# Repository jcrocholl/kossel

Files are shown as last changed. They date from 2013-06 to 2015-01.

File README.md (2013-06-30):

Release status
==============

Most of these parts are now stable and won't change much more.

How to print Mini Kossel
========================

* 3x plate_3x.stl (about 3x80g = 240g of plastic)
* 1x plate_1x.stl (about 50g of plastic)

Links
=====

* Bill of Materials: http://reprap.org/wiki/Kossel
* Mailing list: http://groups.google.com/group/deltabot
* Project history: http://deltabot.tumblr.com

Pay it forward
==============

Johann is offering free printed parts for Mini Kossel:

* I'm going to make some Mini Kossel printed parts kits.
* I'm going to give them away for free (as in beer).
* Some kits may include some non-printed parts.
* Free international shipping is included.
* No delivery schedule, maybe only one kit per month.

But there's no such thing as a free lunch. If you want to receive a
free kit, you must swear by your geek honor:

* To complete your Mini Kossel and tune it well.
* To print two (2) Mini Kossel kits and also give them away for free.
* To make your recipients agree to the same rule.

After giving away the 2 free kits, you may sell printed parts for any
price you want.

If you're interested, please email johann@rocholl.net and let me know
your favorite PLA color and mailing address. If you want to get your
printed parts first, explain why you're more qualified than others to
start giving away high quality printed parts soon.

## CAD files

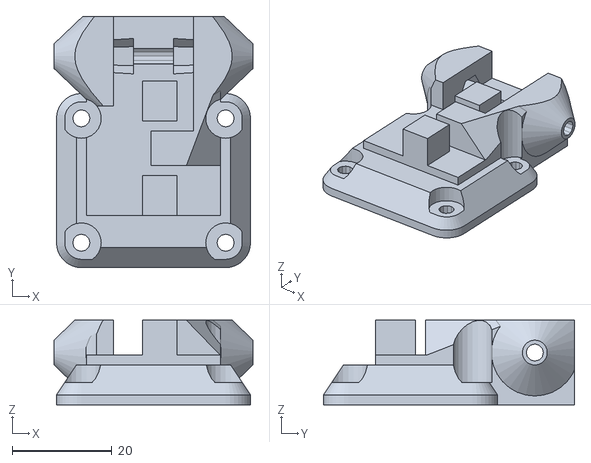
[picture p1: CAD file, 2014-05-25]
carriage_recirculating.stl
40.0 x 50.5 x 17.0

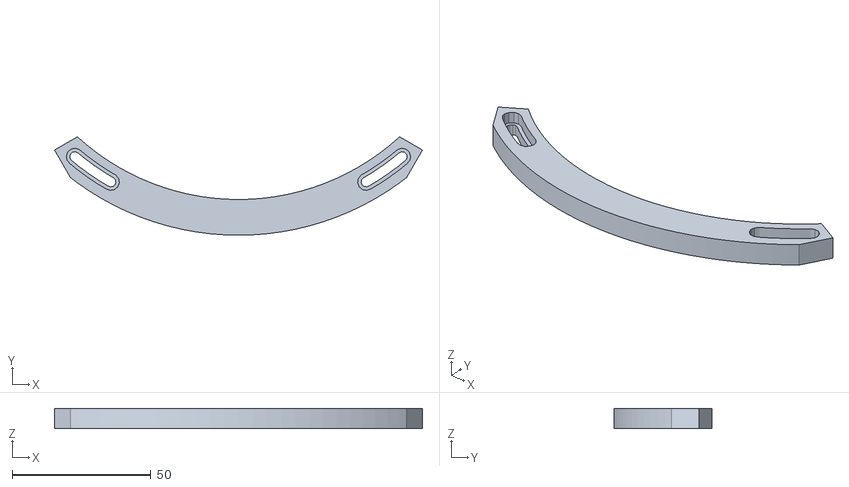
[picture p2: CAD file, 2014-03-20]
glass_frame.stl
132.8 x 35.5 x 7.35

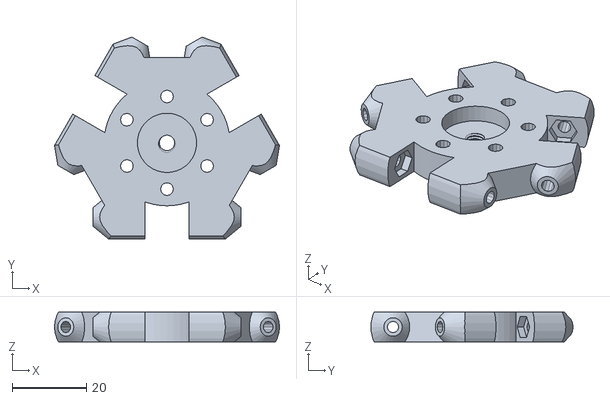
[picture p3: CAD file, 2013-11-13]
effector.stl
60.7 x 54.5 x 8.00

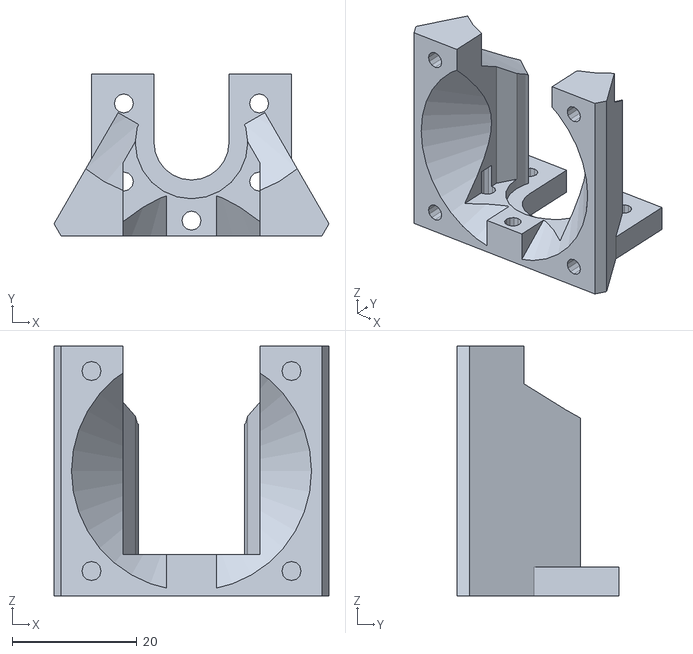
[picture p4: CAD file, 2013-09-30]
hotend_fan.stl
44.0 x 26.0 x 40.0

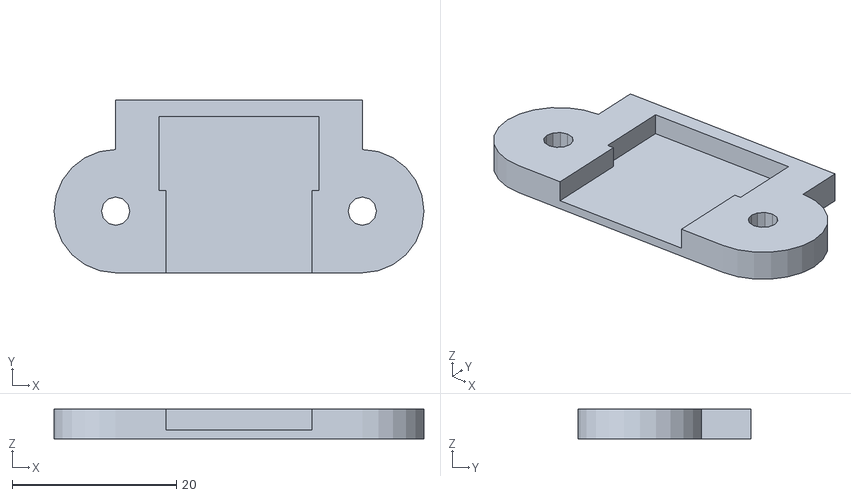
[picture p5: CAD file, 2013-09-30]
switch_holder.stl
45.0 x 21.0 x 3.60

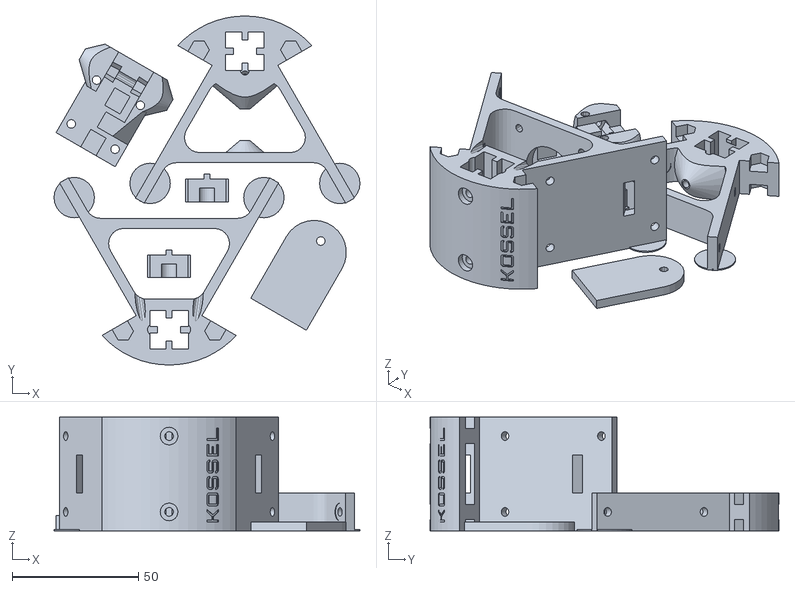
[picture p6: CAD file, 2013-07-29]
plate_3x.stl
121.0 x 138.0 x 45.0

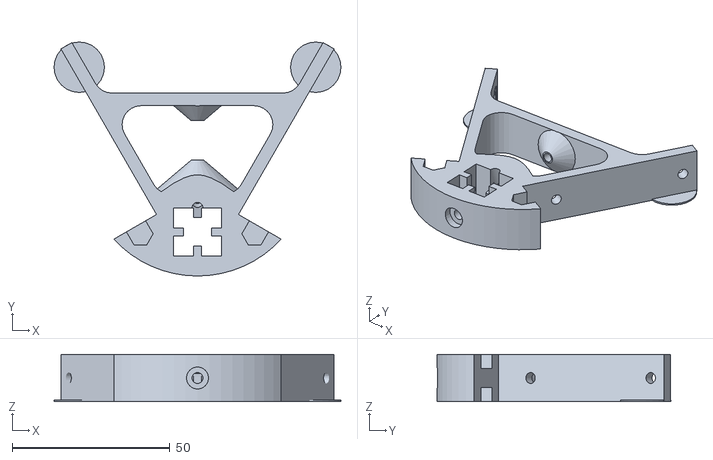
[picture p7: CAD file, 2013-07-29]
frame_top.stl
91.0 x 74.2 x 15.0

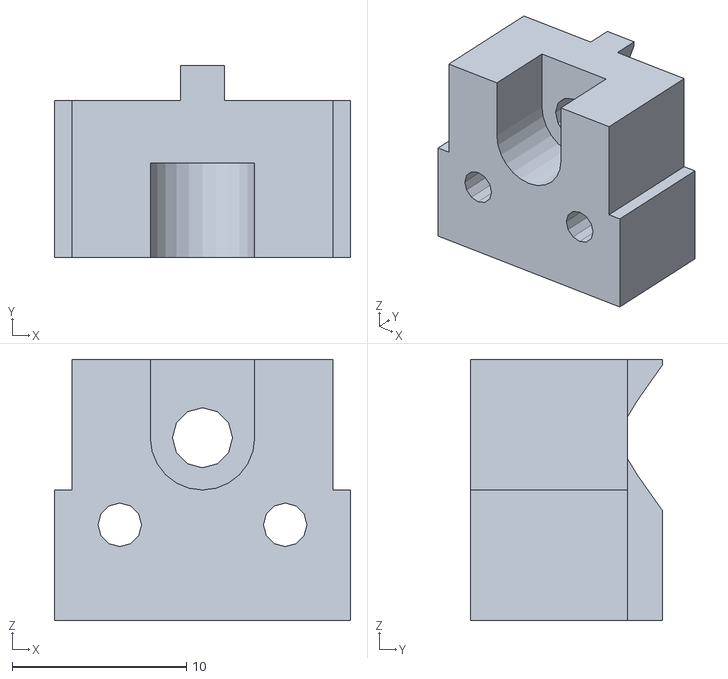
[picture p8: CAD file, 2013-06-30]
endstop.stl
17.0 x 11.0 x 15.0

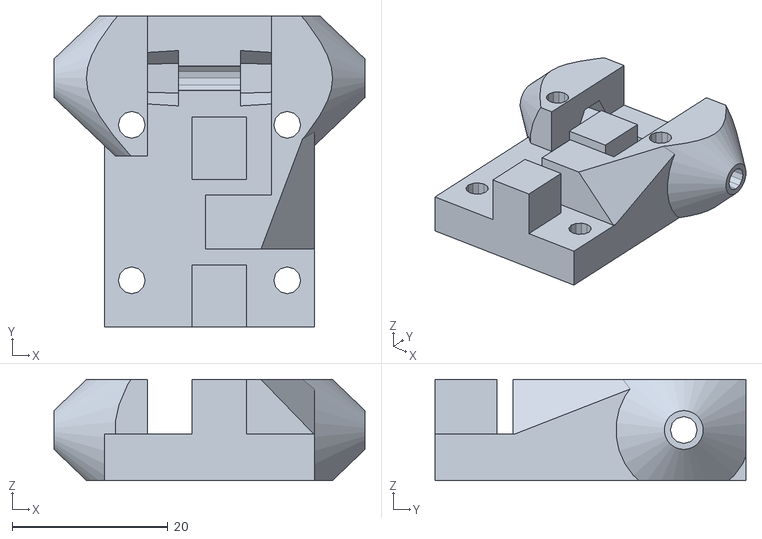
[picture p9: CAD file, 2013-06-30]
carriage.stl
40.0 x 40.0 x 13.0

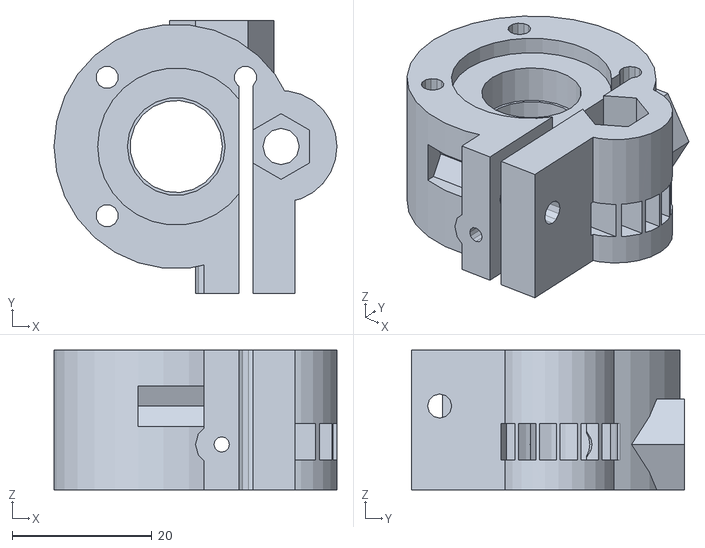
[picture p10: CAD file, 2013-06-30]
extruder.stl
40.5 x 39.0 x 20.0

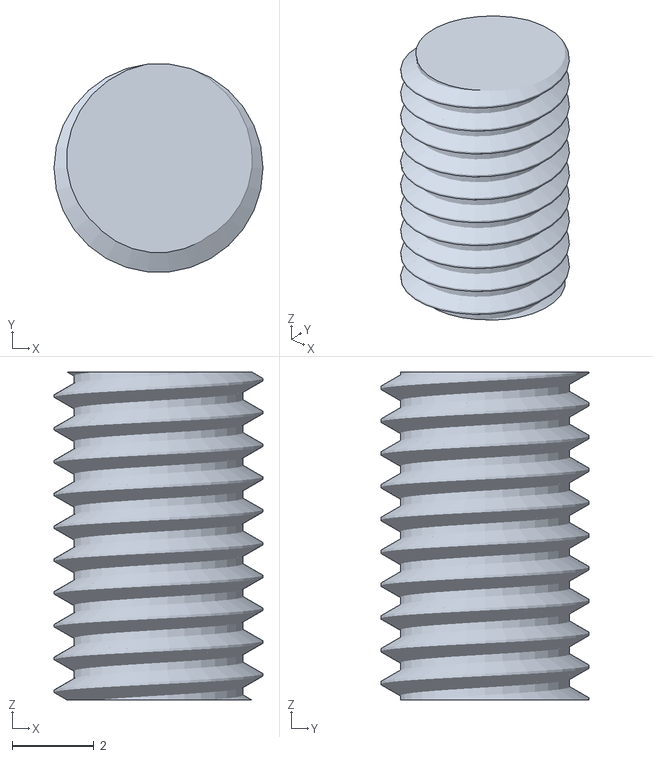
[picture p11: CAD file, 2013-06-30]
m5_internal.stl
5.10 x 5.07 x 8.00

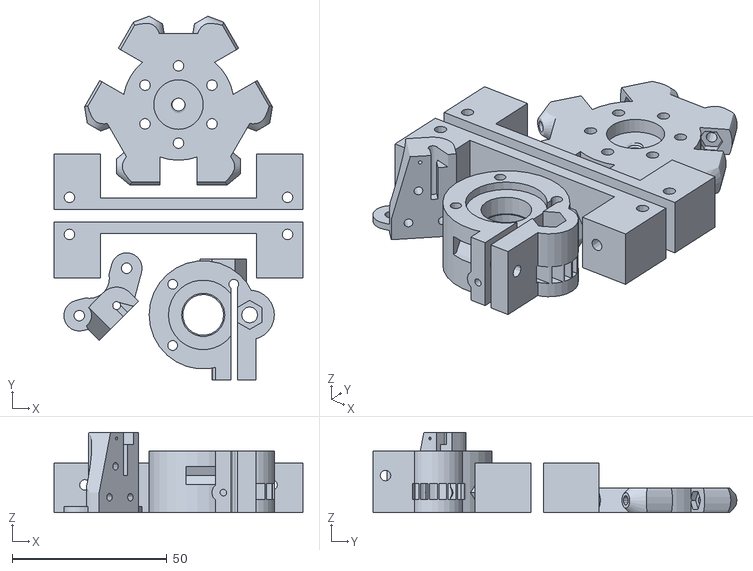
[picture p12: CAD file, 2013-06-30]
plate_1x.stl
80.5 x 117.6 x 26.0

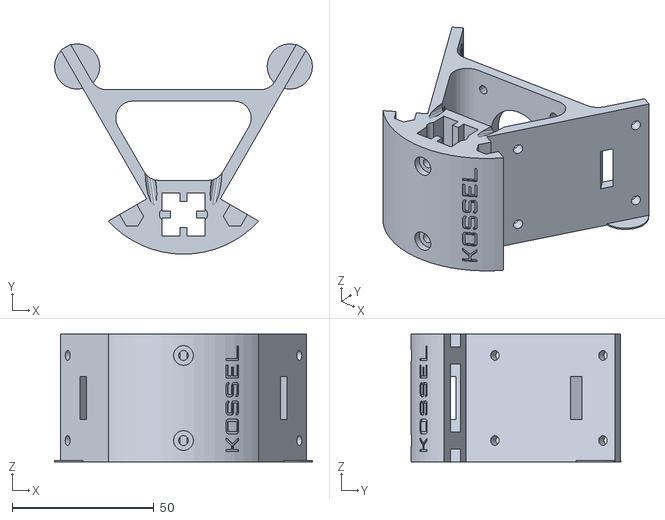
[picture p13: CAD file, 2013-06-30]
frame_motor.stl
91.0 x 74.2 x 45.0

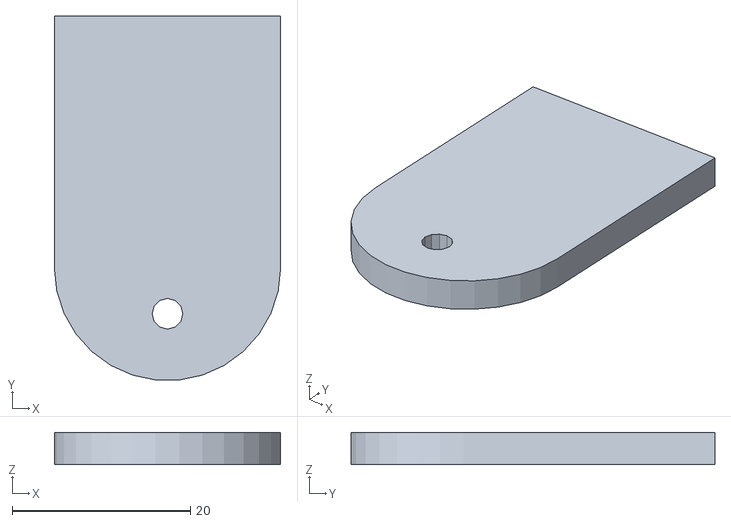
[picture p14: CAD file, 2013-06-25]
glass_tab.stl
25.4 x 40.8 x 3.60

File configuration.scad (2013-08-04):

// Increase this if your slicer or printer make holes too tight.
extra_radius = 0.1;

// OD = outside diameter, corner to corner.
m3_nut_od = 6.1;
m3_nut_radius = m3_nut_od/2 + 0.2 + extra_radius;
m3_washer_radius = 3.5 + extra_radius;

// Major diameter of metric 3mm thread.
m3_major = 2.85;
m3_radius = m3_major/2 + extra_radius;
m3_wide_radius = m3_major/2 + extra_radius + 0.2;

// NEMA17 stepper motors.
motor_shaft_diameter = 5;
motor_shaft_radius = motor_shaft_diameter/2 + extra_radius;

// Frame brackets. M3x8mm screws work best with 3.6 mm brackets.
thickness = 3.6;

// OpenBeam or Misumi. Currently only 15x15 mm, but there is a plan
// to make models more parametric and allow 20x20 mm in the future.
extrusion = 15;

// Placement for the NEMA17 stepper motors.
motor_offset = 44;
motor_length = 47;

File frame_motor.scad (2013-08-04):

include <configuration.scad>;

use <vertex.scad>;
use <nema17.scad>;

$fn = 24;

module frame_motor() {
  difference() {
    // No idler cones.
    vertex(3*extrusion, idler_offset=0, idler_space=100);
    // KOSSEL logotype.
    translate([20.5, -10, 0]) rotate([90, -90, 30])
      scale([0.11, 0.11, 1]) import("logotype.stl");
    // Motor cable paths.
    for (mirror = [-1, 1]) scale([mirror, 1, 1]) {
      translate([-35, 45, 0]) rotate([0, 0, -30])
        # cube([4, 15, 15], center=true);
      translate([-6, 0, 0]) cylinder(r=2.5, h=40);
      translate([-11, 0, 0]) # cube([15, 4, 15], center=true);
    }
    translate([0, motor_offset, 0]) {
      // Motor shaft/pulley cutout.
      rotate([90, 0, 0]) cylinder(r=12, h=20, center=true, $fn=60);
      // NEMA 17 stepper motor mounting screws.
      for (x = [-1, 1]) for (z = [-1, 1]) {
        scale([x, 1, z]) translate([15.5, -5, 15.5]) {
          rotate([90, 0, 0]) cylinder(r=1.65, h=20, center=true, $fn=12);
          // Easier ball driver access.
          rotate([74, -30, 0]) # cylinder(r=1.8, h=60, $fn=12);
        }
      }
    }
    translate([0, motor_offset, 0]) rotate([90, 0, 0]) % nema17();
  }
}

translate([0, 0, 22.5]) frame_motor();

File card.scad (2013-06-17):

scale([-1, 1, 1]) difference() {
  minkowski() {
    cube([66, 29, 0.2], center=true);
    cylinder(r=10, h=0.2, $fn=24);
  }
  difference() {
    translate([1, -4, 0]) scale([0.2, 0.2, 1]) import("logotype.stl");
    # translate([-17.2, 0, 0]) cube([1, 20, 20], center=true);
  }
}

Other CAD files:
frame_extruder.stl
logotype.stl
power_supply.stl
retractable.stl
carriage.scad
Orbitron_Medium.scad
card.stl
carriage_recirculating.scad
effector.scad
endstop.scad
extruder.scad
frame_extruder.scad
frame_power_supply.scad
frame_top.scad
glass_frame.scad
glass_tab.scad
hotend_fan.scad
logotype.scad
m5_internal.scad
microswitch.scad
nema17.scad
pg35l_extruder.scad
plate_1x.scad
plate_3x.scad
power_supply.scad
retractable.scad
spool.scad
switch_holder.scad
threads.scad
vertex.scad

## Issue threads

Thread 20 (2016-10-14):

Kossel Mini Bed Level Problem

grimes27, 2016-10-14:
I'm very new to this but, I have my Kossel Mini up and running my only problem is it seems if I run the auto-level before I start printing it doesn't do anything because the extruder is running into the bed.  From all the checking I've done my print bed is very level but if I put my extruder at 1mm above the print bed and move the extruder roughly 40mm in any direction X+, X-, Y+ or Y- it runs into the print bed.  So either I have a convex lens for a printbed, which I doubt, because I have the same problem if I flip the bed around, or the motion of my printer is out of whack.  Any ideas what's going on or how to fix this?

kd0aij, 2016-10-14:
This is not actually an issue with the code. It sounds more like you skipped a critical part of the calibration process. Look at step #3 here: http://ladvien.github.io/robots/kossel-mini-calibration/ for adjusting delta_radius. (I just did a quick google search; you didn't mention which firmware you are using)

grimes27, 2016-10-14:
Yes, I didn't have these instructions when I set up my kossel.  I used the
one from Blomker industries and they didn't say anything about the concave
or convex surface.  Thank you very much for this.  I am using Marlin
Firmware too!

On Fri, Oct 14, 2016 at 12:16 PM, Mark Whitehorn <notifications@github.com>
wrote:

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

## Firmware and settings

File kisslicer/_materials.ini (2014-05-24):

[Rostock PLA]
g_code_matl=3B204D617962652073657420736F6D65206D6174657269616C2D737065636966696320472D636F64653F
fan_Z_mm=0.5
fan_loops_percent=100
fan_inside_percent=0
fan_cool_percent=100
temperature_C=185
keep_warm_C=120
first_layer_C=195
bed_C=0
sec_per_C_per_C=0.00964207
flow_min_mm3_per_s=0.1
flow_max_mm3_per_s=20
destring_suck=8
destring_prime=8
destring_min_mm=3
destring_trigger_mm=20
destring_speed_mm_per_s=80
Z_lift_mm=0.2
min_layer_time_s=15
wipe_mm=3
cost_per_cm3=0
flowrate_tweak=1
fiber_dia_mm=1.75
color=4288872448

[Mini Kossel PLA]
g_code_matl=3B204D617962652073657420736F6D65206D6174657269616C2D737065636966696320472D636F64653F
fan_Z_mm=0.5
fan_loops_percent=100
fan_inside_percent=0
fan_cool_percent=100
temperature_C=230
keep_warm_C=120
first_layer_C=240
bed_C=0
sec_per_C_per_C=0.00964207
flow_min_mm3_per_s=0.1
flow_max_mm3_per_s=20
destring_suck=10
destring_prime=10
destring_min_mm=2
destring_trigger_mm=20
destring_speed_mm_per_s=100
Z_lift_mm=0.2
min_layer_time_s=15
wipe_mm=3
cost_per_cm3=0
flowrate_tweak=1
fiber_dia_mm=1.75
color=4288872448

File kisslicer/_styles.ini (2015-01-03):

[Mini Kossel]
layer_thickness_mm=0.2
extrusion_width_mm=0.4
num_loops=3
skin_thickness_mm=0.6
infill_extrusion_width=0.35
infill_density_denominator=1
stacked_layers=1
use_destring=1
use_wipe=1
loops_insideout=1
infill_st_oct_rnd=0
inset_surface_xy_mm=0.1
seam_jitter_degrees=10
seam_depth_scaler=1

[Rostock]
layer_thickness_mm=0.2
extrusion_width_mm=0.5
num_loops=3
skin_thickness_mm=0.8
infill_extrusion_width=0.5
infill_density_denominator=1
stacked_layers=1
use_destring=1
use_wipe=1
loops_insideout=1
infill_st_oct_rnd=0
inset_surface_xy_mm=0
seam_jitter_degrees=60
seam_depth_scaler=1

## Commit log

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2012-09-29 Spool for fishing line on NEMA17 stepper with M3x8 screws.
    [spool.scad]
2012-09-30 Slic3r 0.9.3 doesn't need oversized holes like 0.8.4 did.
    [spool.scad]
2012-10-03 Adjustments for Slic3r 0.9.3 which seems to make more accurate parts than 0.8.4.
    [corner.scad, frame_motor.scad, spool.scad]
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2012-10-10 Diagonal filament tunnel to spool from the edge to the middle.
    [spool.scad]
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2012-10-14 Improved OpenBeam roller with 4 horizontal adjustment screws and integrated attachment for ball joints.
    [roller.scad]
2012-10-14 Added adjustable endstop screw to roller, adjusted holes.
    [roller.scad]
2012-10-18 Separate fishline tunnel parallel to motor shaft, to improve centering accuracy.
    [spool.scad]
2012-10-18 Removed some plastic that was obstructing the range of motion for the ball joints.
    [roller.scad]
2012-10-18 New triangle (quasi-L-shaped) frame vertex for top corners.
    [frame_cheek.scad]
2012-10-19 Put the adjustable endstop screw on the outside.
    [roller.scad]
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2012-10-21 Added ZM micro switch holder on the cheek outside.
    [frame_cheek.scad]
2012-10-21 Added slightly more plastic around the ball joint attachment.
    [roller.scad]
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2012-10-29 Adjusted corner screw holes for thicker 3.6mm brackets.
    [corner.scad]
2012-11-01 New fishline tensioner with a regular cheap 608 bearing (not flanged).
    [tensioner_608.scad]
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2012-11-05 Tightened M3 nut trap and OpenBeam groove clip.
    [configuration.scad, tensioner_608.scad]
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2012-11-12 Increased thickness to 3.6mm and removed middle screw.
    [frame_motor.scad]
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2012-11-15 Smaller attachments for ball joints with M3x20 screws.
    [effector.scad]
2012-11-17 Shorter attachments for diagonal rods. Adjustable endstop screw and fishline attachment only on left side roller.
    [roller.scad]
2012-11-17 Rotate top tensioner 608 bearing 22.5 degrees to add more clearance for the return fishline.
    [tensioner_608.scad]
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2012-11-18 Screw holes in frame_motor no longer need to be countersunk.
    [frame_motor.scad]
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2012-11-18 Move frame thickness to configuration.scad. Update corner.scad for the thickness change from 3 to 3.6 mm, thanks to John Driggers.
    [configuration.scad, corner.scad, frame_cheek.scad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]
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2012-11-25 Split left and right roller into separate files.
    [roller.scad, roller_left.scad, roller_right.scad]
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2013-01-09 Very rough draft: experimental elastic X-shaped carriage for 4 delrin roller wheels.
    [four_wheels.scad]
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2013-01-13 Added some space for shrink wrap around 623 bearings. Also merged roller_left.scad and roller_right.scad back into roller.scad.
    [configuration.scad, roller.scad, roller_left.scad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]
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2013-01-24 Larger end effector to move diagonal carbon rods out of the way for PG35L extruder motor.
    [configuration.scad, effector.scad]
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2013-02-14 Experimental: add small pads to the curling ends to improve adhesion to unheated print bed.
    [frame_integrated.scad]
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2013-03-02 pg35l_extruder: Place drive gear to exactly contact the filament
    This change reduces the offset from 7mm to 6.375mm.
    Also add some notes of measured hobbed pulley sizes.
    [pg35l_extruder.scad]
2013-03-02 pg35l_extruder: Simplify the filament funnel code
    It's pretty odd when you change a drive gear OD and the funnel size
    changes. Re-work funnel code to be easier to understand and change.
    [pg35l_extruder.scad]
2013-03-02 pg35l_extruder: Rename filament_id to filament_dia
    It's really an OD, not an ID, anyway.
    Conflicts:
    pg35l_extruder.scad
    [pg35l_extruder.scad]
2013-03-02 pg35l_extruder: Separate the filament size and filament hole sizes
    This is necessary when the drive gear is positioned based on the
    filament size. Using the true filament dia rather than the hole
    dia moves the drive gear slightly closer to the filament.
    [pg35l_extruder.scad]
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2013-04-12 Start adding STL files because github now includes a working STL viewer.
    [frame_motor.stl, frame_top.stl]
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2013-04-17 Try Orbitron Medium (weight 500) instead of Orbitron Black (weight 900) because the letter S looked like 8 when printed.
    [Orbitron_Medium.scad, frame_motor.stl, logotype.scad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]
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2013-04-18 Wider space for idler bearings, to allow running the timing belt closer to the stepper motor.
    [frame_motor.scad, frame_motor.stl, frame_top.scad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]
2013-04-18 Refactored vertex module into separate file, to allow changing frame_top.scad without rebuilding frame_motor.stl.
    [frame_motor.scad, frame_top.scad, vertex.scad]
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2013-04-27 Ultra compact end effector with integrated 16mm groove mount for J-Head or MakerGear hotends.
    [effector.scad, effector.stl]
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2013-05-03 Shave some plastic off the vertical carriage to avoid touching diagonal push rods (carbon tubes).
    [carriage.scad, carriage.stl, frame_motor.stl]
2013-05-03 Change belt clamp angle from 90 to 60 degrees to avoid skipping.
    [carriage.scad, carriage.stl]
2013-05-04 Improved belt clams to avoid slipping. Added vertical calibration screw.
    [carriage.scad, carriage.stl]
2013-05-04 Replace some tabs with spaces.
    [carriage.scad, frame_motor.scad, frame_top.scad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]
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2013-05-28 Simple print surface holder for use with Scotch 3M Restickable Tabs For Mounting.
    [glass_tab.scad, glass_tab.stl]
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2013-05-28 Removed some obsolete files from this branch, https://github.com/jcrocholl/kossel/tree/legacy still has some of them.
    [Orbitron_Black.scad, four_wheels.scad, roller.scad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]
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2013-06-17 Fixed #6 by adding channels for easier ball driver access to NEMA 17 stepper motor screws.
    [frame_motor.scad, frame_motor.stl]
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2013-06-20 Slightly bigger access for ball driver to NEMA17 stepper motor mounting screws.
    [frame_motor.scad, frame_motor.stl]
2013-06-20 Fixed #10 by removing unused vertical calibration screw on carriages.
    [carriage.scad, carriage.stl]
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2013-06-21 Shorter channel to the extruder push-fit connector.
    [extruder.scad, extruder.stl]
2013-06-22 Changed frame_top idler bolt from M4 to M3 for use with F623ZZ bearings.
    [frame_top.scad, frame_top.stl]
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2013-06-22 One third of Mini Kossel (6 parts) on a round plate, about 160 mm diameter.
    [plate_3x.scad, plate_3x.stl]
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2013-06-30 Fixed overlapping nut tunnel facets in vertex.scad which were causing Slic3r errors.
    [frame_motor.stl, frame_top.stl, plate_3x.stl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]
2013-06-30 Stop removing degenerate (zero area) faces because that also makes some models non-manifold.
    [frame_motor.stl]
2013-06-30 Slic3r no longer complains about plate_3x.
    [plate_3x.stl]
2013-06-30 Slic3r no longer complains about plate_1x.
    [m5_internal.stl, plate_1x.stl]
2013-06-30 Slic3r no longer complains about extruder.
    [extruder.stl]
2013-06-30 Slic3r no longer complains about carriage.
    [carriage.stl]
2013-06-30 Slic3r no longer complains about endstop.
    [endstop.stl]
2013-06-30 Slic3r no longer complains about frame_top.
    [frame_top.stl]
2013-07-29 Adjusted idler bearing M3 bolt and nyloc trap for tighter fit.
    [frame_top.scad, frame_top.stl, plate_3x.stl]
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2013-11-13 Increased clearance for inserting Nyloc nuts.
    [effector.scad, effector.stl]
2014-03-20 Printed frame surrounding round glass, to be attached with clear tape. This should prevent sideways wobble of the print surface but allow precise FSR autolevel.
    [glass_frame.scad, glass_frame.stl]
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2014-11-29 Avoid printing incomplete Gcode: write to tmp file first, then rename atomically.
